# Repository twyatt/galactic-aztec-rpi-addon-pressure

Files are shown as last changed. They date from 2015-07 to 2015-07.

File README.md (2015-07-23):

# About
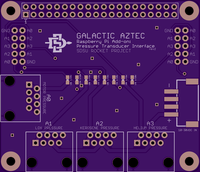
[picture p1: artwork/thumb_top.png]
OSHPark PCB Top Thumbnail

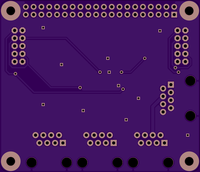
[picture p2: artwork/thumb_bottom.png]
OSHPark PCB Bottom Thumbnail


Custom Raspberry Pi Add-on board used as a pressure transducer interface board for the [Galactic Aztec] rocket. The board has a single JST XH port for power input (Supply Voltage), 4 ethernet ports for interfacing with custom [pressure transducer connector boards] and 2 header pin ports (pressure transducer stepped-down voltage output) for optional ribbon cable connectivity.

## Wiring
The ethernet ports adhere to the following [T-568B] wiring configuration:

| Pin | Color | Function |
|:---:|:---:|:---:|
| 1 | Orange/White | Signal |
| 2 | Orange | Signal |
| 3 | Green/White  | |
| 4 | Blue | Supply Voltage |
| 5 | Blue/White | Supply Voltage |
| 6 | Green | |
| 7 | Brown/White  | Ground |
| 8 | Brown | Ground |

## Launch
For the [Galactic Aztec April 18th, 2015 launch], the following pressure transducers were used:
* 3 x [P51-500-A-A-I36-5V-000-000]
  * LOX, Kerosene and motor pressure
* 1 x [MSP-300-2K5-P-4-N-1]
  * Helium pressure

Custom EagleCAD parts on this board can be found in the [SDSU Rocket Eagle Libraries].

# Bill of Materials
| Qty | Description | Part Number | Vendor |
|:---:|---|---:|---|
| 4 | Jack RJ45 CAT5/CAT5e | [380-1046-ND] | DigiKey  |
| 1 | Header JST XH 2.5mm 4-pos Right Angle SMD | [455-2262-1-ND] | DigiKey  |
| 2 | Header Male 2x5 0.1" Pitch | [609-3236-ND] | DigiKey  |
| 4 | Resistor 10kΩ 1/4W 1% 0603 | [P10KBYCT-ND] | DigiKey  |
| 4 | Resistor 15kΩ 1/4W 1% 0603 | [RHM15.0KADCT-ND] | DigiKey  |
| 1 | Header Stacking 2x20 Tall 23mm | [1979] | Adafruit |

[Galactic Aztec]: http://rocket.sdsu.edu/rockets
[pressure transducer connector boards]: https://github.com/twyatt/galactic-aztec-pressure-transducer-connector
[T-568B]: https://en.wikipedia.org/wiki/TIA/EIA-568#Wiring
[Galactic Aztec April 18th, 2015 launch]: https://github.com/twyatt/galactic-aztec-launch-data
[P51-500-A-A-I36-5V-000-000]: http://www.ssi-sensors.com/pdfs/Pressure%20Sensors/P51/PS-AN2_FAMILY%20PRODUCT%20OVERVIEW.pdf
[MSP-300-2K5-P-4-N-1]: http://www.mouser.com/ds/2/418/MSP300-710393.pdf
[SDSU Rocket Eagle Libraries]: https://github.com/twyatt/SDSURocket-Eagle-Libraries
[380-1046-ND]: http://www.digikey.com/product-detail/en/SS-7188-NF/380-1046-ND/388308
[455-2262-1-ND]: http://www.digikey.com/product-detail/en/S4B-XH-SM4-TB(LF)(SN)/455-2262-1-ND/1651060
[609-3236-ND]: http://www.digikey.com/product-detail/en/67997-210HLF/609-3236-ND/1878541
[P10KBYCT-ND]: http://www.digikey.com/product-detail/en/ERJ-PA3F1002V/P10KBYCT-ND/5036115
[RHM15.0KADCT-ND]: http://www.digikey.com/product-detail/en/ESR03EZPF1502/RHM15.0KADCT-ND/1983758
[1979]: https://www.adafruit.com/product/1979

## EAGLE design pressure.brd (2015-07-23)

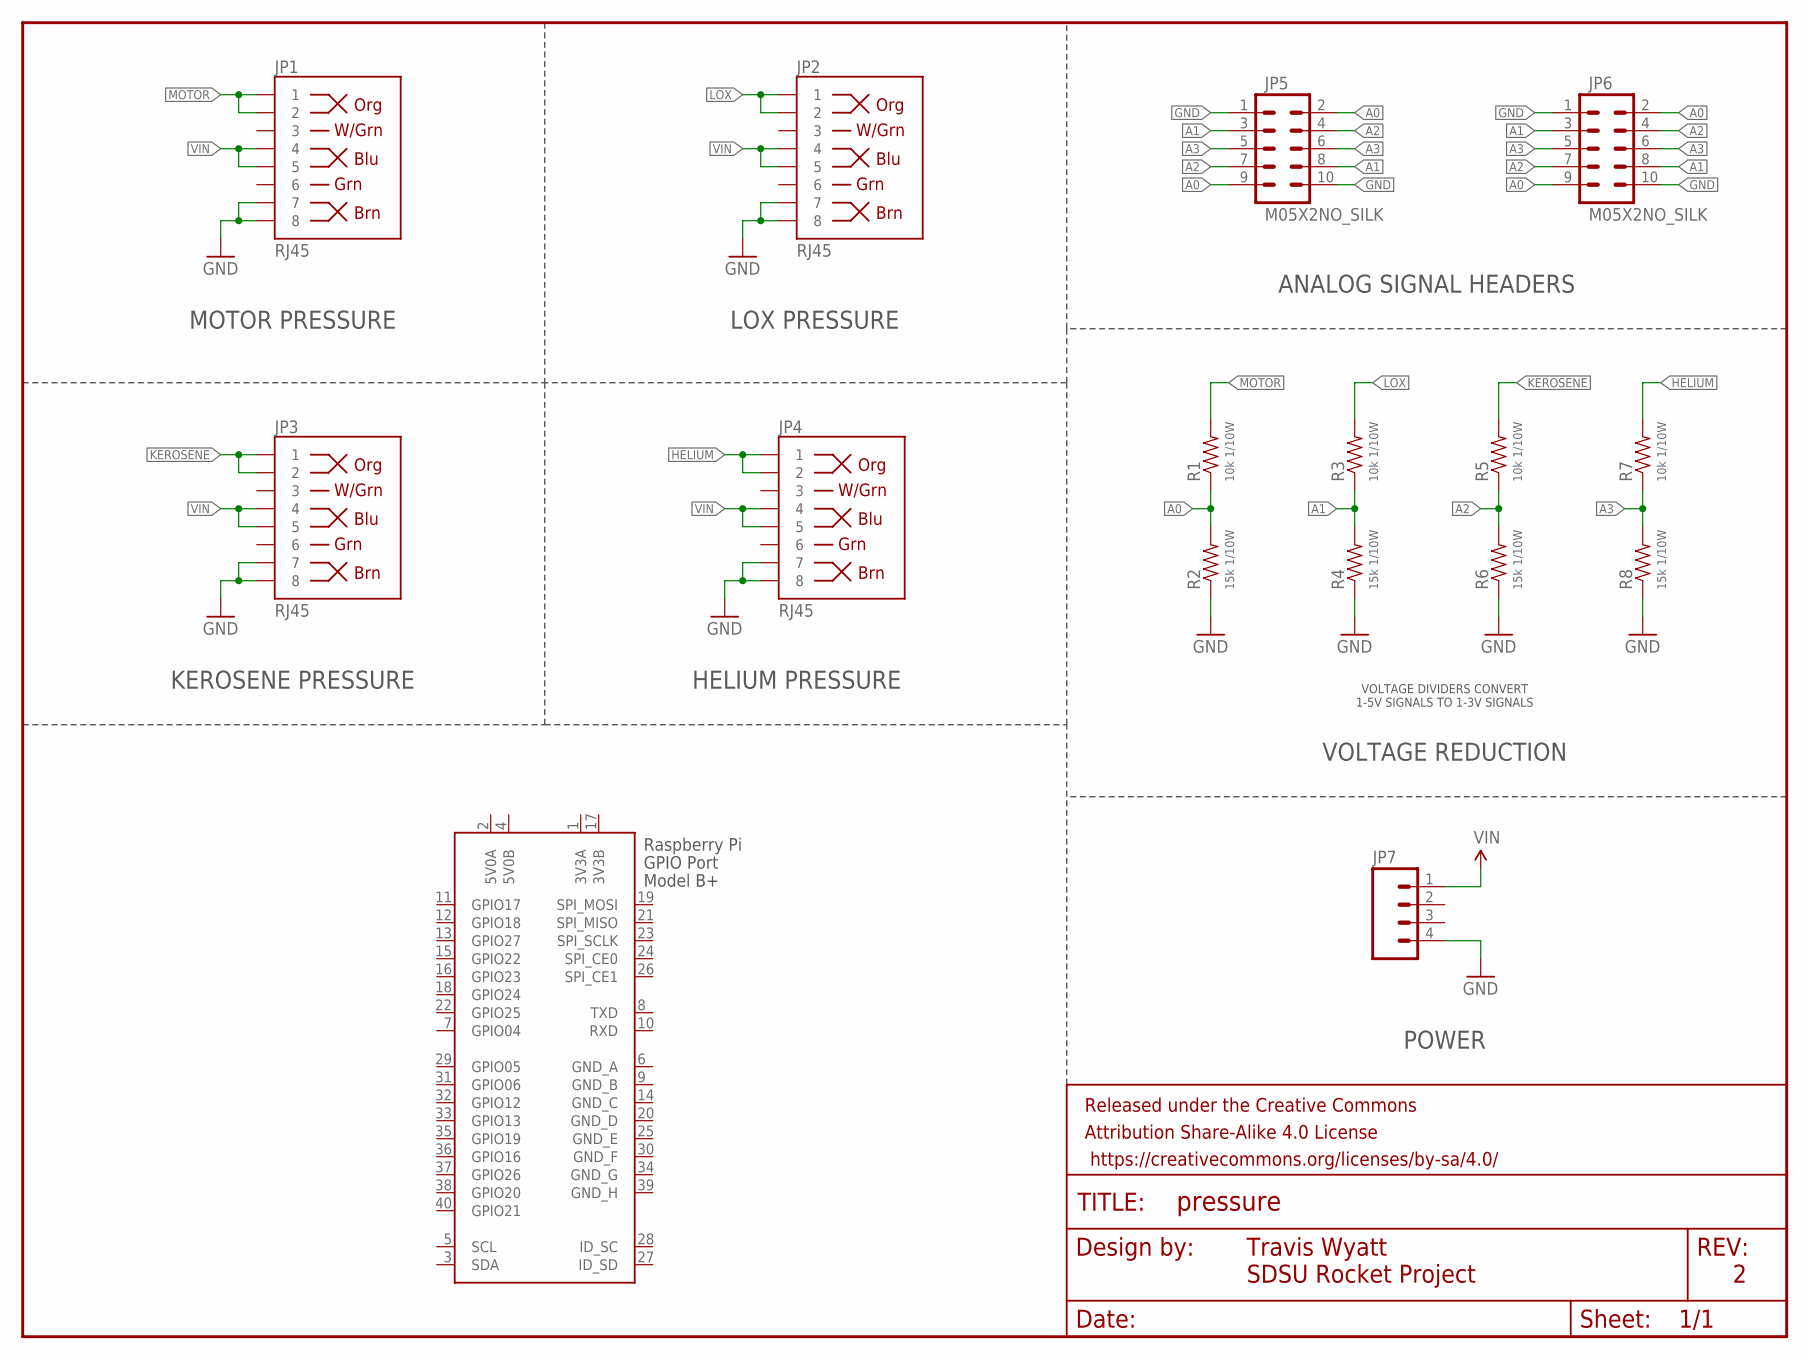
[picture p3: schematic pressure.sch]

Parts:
FRAME1: FRAME-LETTER; CREATIVE_COMMONS
JP1, JP2, JP3, JP4: RJ45; RJ45-8
JP5, JP6: M05X2NO_SILK; 2X5_NOSILK
JP7: JST-4POS-2.5MM; S4B-XH-SM4-TB
R1, R3, R5, R7: 10k 1/10W; 0603-RES
R2, R4, R6, R8: 15k 1/10W; 0603-RES
X1: RASPI_BOARD_B+#_H; RASPI_BOARD_B+HAT

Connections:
3V3A: X1.1 (3V3A)
3V3B: X1.17 (3V3B)
5V0A: X1.2 (5V0A)
5V0B: X1.4 (5V0B)
A0: JP5.2, JP5.9, JP6.2, JP6.9, R1.1, R2.2
A1: JP5.3, JP5.8, JP6.3, JP6.8, R3.1, R4.2
A2: JP5.4, JP5.7, JP6.4, JP6.7, R5.1, R6.2
A3: JP5.5, JP5.6, JP6.5, JP6.6, R7.1, R8.2
GND: JP1.7, JP1.8, JP2.7, JP2.8, JP3.7, JP3.8, JP4.7, JP4.8, JP5.1, JP5.10, JP6.1, JP6.10, JP7.4, R2.1, R4.1, R6.1, R8.1
GND_A: X1.6 (GND_A)
GND_B: X1.9 (GND_B)
GND_C: X1.14 (GND_C)
GND_D: X1.20 (GND_D)
GND_E: X1.25 (GND_E)
GND_F: X1.30 (GND_F)
GND_G: X1.34 (GND_G)
GND_H: X1.39 (GND_H)
HELIUM: JP4.1, JP4.2, R7.2
KEROSENE: JP3.1, JP3.2, R5.2
LOX: JP2.1, JP2.2, R3.2
MOTOR: JP1.1, JP1.2, R1.2
VIN: JP1.4, JP1.5, JP2.4, JP2.5, JP3.4, JP3.5, JP4.4, JP4.5, JP7.1

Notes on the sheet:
ANALOG SIGNAL HEADERS
Travis Wyatt
SDSU Rocket Project
MOTOR PRESSURE
KEROSENE PRESSURE
LOX PRESSURE
HELIUM PRESSURE
POWER
VOLTAGE REDUCTION
VOLTAGE DIVIDERS CONVERT 1-5V SIGNALS TO 1-3V SIGNALS

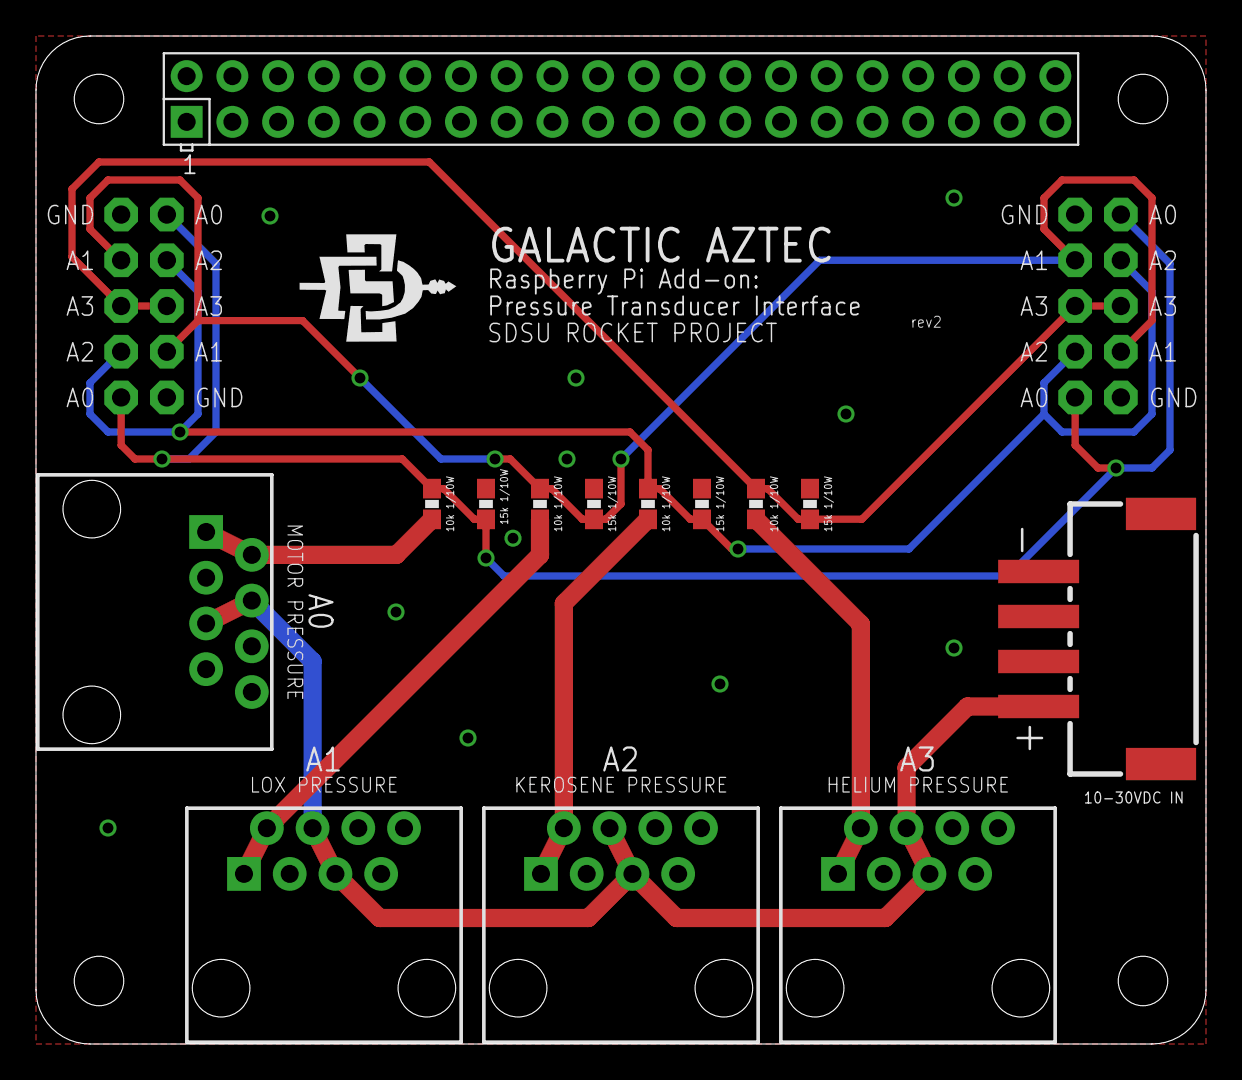
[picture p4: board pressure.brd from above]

Board: 2 copper layers, 65.0 x 56.0 mm, 17 parts (0 on the bottom side), 10 nets.

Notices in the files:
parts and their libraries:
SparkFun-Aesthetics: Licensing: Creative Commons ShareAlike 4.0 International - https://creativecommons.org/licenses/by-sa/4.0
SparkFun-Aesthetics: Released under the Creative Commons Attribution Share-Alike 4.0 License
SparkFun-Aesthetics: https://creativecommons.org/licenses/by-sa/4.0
